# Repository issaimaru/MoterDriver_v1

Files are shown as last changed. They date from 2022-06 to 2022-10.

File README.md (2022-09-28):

# DriveUnit Bseries
**[自作電源基板](https://github.com/Issaimaru/PowerSupply_v1)に刺して使う80A級モータードライバ**<br>
**[DUB with 遠野](https://github.com/Issaimaru/DUB_with_Tono)を使って遠野に刺すこともできます**<br>
**動作電圧 8[V]~30[V]**<br>
**PWM周波数 ~250kHz**<br>
**duty比 100%対応**<br>
**電圧監視機能搭載**<br>
**LAP/SM方式での駆動が可能**<br>
**制作期間:2022/01/18頃～**<br>
**名前:DriveUnit Bseries**<br>

## バージョンに対応するドキュメント
- ver1.0-->[README_v1.md](https://github.com/Issaimaru/MoterDriver_v1/blob/master/README_v1.md)
- ver2.0-->[README_v2.md](https://github.com/Issaimaru/MoterDriver_v1/blob/master/README_v2.md)

## 前モータードライバ(野獣)との違い
野獣がノートパソコンで，DUBがゲーミングパソコンと例えるとわかりやすいと思います．(やや過言かもしれないです...)<br>
野獣ができることは基本的にDUBでもできますし，野獣でできないような機能もDUBにはありますが，値段とサイズ的にはDUBが劣ります．<br>
- **PWM比1.0での動作が可能**<br>
このモータードライバで使用しているA3921というゲートドライバは，ハイサイドにチャージポンプを内蔵しています．そのため，PWM比が1.0の近くであっても正常に動作することができます．<br>

- **動作周波数帯域が増えた**<br>
    > 100Hz以上10000Hz未満なら一応動く。一番特性がいいのは2kHz。<br>
 
  富山本郷メカテック部wikiの野獣の説明にはこのように書いてありますが，20kHzまでは人間の可聴域なので20kHz以下でモータを駆動させると大きな音がモータから発せられてしまいます．      <br>DriveUnit Bseries(以下，DUBといいます．)は ~~**計算上では**100kHzでも動作します．これは実験で確かめます．~~　<br>
  実験したところ，mbedではPWM周波数に比例してPWM分解能が小さくなるため，20kHzを超えると明らかにモーターの動作が不安定になります．
  <br>STM32CubeIDEからHALドライバーを使用し，タイマーの設定を変更することでこの問題を解消することができますが([ここ](https://qiita.com/ShunHattori/items/68f099f1d77702d2535d)を参照)，普通はオンラインコンパイラから制御しますよね...(実際にHALドライバーを使用してやってみましたが色々めんどくさいです)<br>
  上記の問題から，HALドライバーを使用せずにこのモータードライバを使用する場合は10kHz~20kHzで使用することを推奨します．(可聴域内ですが，音は聞こえないです．)<br>
  また，HALドライバーを使用する場合は250kHz以下の周波数で使用するようにしてください．
  
- **LAP/SM方式の切り替えが可能**<br>
このモータードライバで使用しているA3921というゲートドライバの配線をうまくしてやると，PWM方式(LAP/SM)をスイッチ一つで切り替えることが実現できます．SM方式はPWM比がそのまま回転数と比例し，効率がよく，低周波でも線形性が比較的保たれるのに対して，LAP方式は正転と逆転の比率を調整してモータの回転方向と回転速度を変化させる方式であり，Duty比50%でモーターが停止するという違いがあります．

- **定格電圧が大きくなった**<br>
モータードライバでは逆起電力が生じるため加える電圧の2倍程度のマージンを取る必要がある(と他高専のOBの方からアドバイスを頂きました．)<br>そのため， $V_{DS}$ が30 $V$ のFETを使用し，コンデンサやゲートドライバの耐圧も30 $V$ 以上になるように選定しました．<br>また，パスコンには(これも他高専のOBの方のアドバイスで)高分子コンデンサを使用しました．<br>そのため，野獣よりも逆起電力に強くなりましたが，6セルのリポバッテリー等を使って急減速をすると逆起電力で普通に30 $V$ を超えます(上の「特性」を参照)．そのため，6セルのリポバッテリー等を使用する場合は電源ラインをオシロスコープで確認して，逆起電力で30 $V$ を超えないか確認することを推奨します．

- **ボタンでモータを制御できるようになった**<br>
MD10Cのように，ボタンでモータの正転，逆転を制御できるようにしました．

- **定格電流が大きくなった**<br>
DUBでは(これも実験で確かめますが)最大で連続80 $A$ の電流を流すことができます．しかし，ハピロボ以降のロボコンは30 $A$ 以下という電流制限があるため，電源基板側にリセッタブルヒューズがついています．そのためあまり意味はありません．<br>

- **電圧監視機能が付いた**<br>
これもA3921の機能ですが，ハイサイドのFETの $V_{DS}$ 間の電圧を監視することによって万が一短絡した場合でもすぐに動作を止めてくれるほか，オーバーヒートしてるような状態なども検知してFFXのLEDを光らせることで警告してくれます．<br>
A3921のデータシートから取ってきたものですが，各FFピンの出力に対する説明は以下の表の通りとなっています．<br>


- **逆接しにくくなった**<br>
エッジコネクタは物理的に逆接が不可能な状態になっていませんが，野獣は勿論のことこのモータードライバも逆接すると燃えます．<br>
そのため，このモータードライバと電源基板では三角の印をつけることで接続する向きが把握しやすいようにしました．<br>

## はんだ付けの仕方
長くなるのでたたみます．
<details><summary>はんだ付けの仕方</summary>
まず初めに，このモータードライバのはんだ付けはとてもめんどくさいです．<br>
なぜなら，はんだごてではんだ付けするにはあまりにも小さすぎる部品を使っているため，リフローをする必要があるからです(恐らく部内でリフローする基板はこれが初めて)．<br>
といっても，部内にはリフローオーブンなんてないので....<br>

ホットプレートリフロー<br>
ホットプレートを使用したホットプレートリフローではんだ付けしています．<br>
ていっても，基板は両面ありますが片面をホットプレートリフローしてもう片面も同じようにやろうとすると，はんだ付け済みの面が先に温まってしまうので両面をこの方法ですることはできません．そこでもう片面は.......<br>

61UcROmBZZL _SL1500_
ヒートガンを使用したヒートガンリフローではんだ付けしています．<br>
そのため，~~本当にめんどくさい~~ですが一気にはんだ付けできるため手はんだとどっちがめんどくさいかと聞かれるとどっちもどっちかなと思います．<br>
とりあえず，はんだづけの仕方を書いておかないと正直量産は自分以外に難しくなってしまうのでここに書いておきます．<br>

まず，ホットプレートリフローをする面は裏面(下の画像で示している面)です．<br>
<br>

理由は，この基板ではんだ付けが一番難しい部品がこの面のICで，こっちの面をヒートガンでリフローするとリフローの風ではんだが飛んで隣同士がくっついてしまう可能性があるからです．<br>
ホットプレートリフローについては[ここ](https://qiita.com/azusa9/items/a2fc4f26799de5588c58)を見ればやり方は完全理解することができると思いますが，一応自分流のやり方を書いておきます．<br>

1. いらない基板を3つ用意してDUBを囲うように配置する．
    <br>
    画像のように，DUBより大きめの基板をDUBの周りに配置します．<br>

1. テープ(できれば養生)で固定する．
    <br>
    こんな感じでDUBが動かないように固定してください．あとから剥がすので養生の方がいいです．自分は家に養生テープがなかったのでセロハンテープでやってます．

1. ステンシル(メタルマスク)をパッドに合わせて上だけテープで固定する
    <br>
    ステンシルの穴がパッドにしっかりと合うようにして，上だけをテープで固定します．<br>
    上だけを固定する理由は後で説明します．

1. クリーム半田をいらないカード等で伸ばしながら塗る<br>
    
    417DpgW1wLL _AC_<br>
    部室に画像のようなクリームはんだがあると思います．(なければ買ってください．自分は[ここ](https://www.amazon.co.jp/gp/product/B09QCQ12RV/ref=ppx_yo_dt_b_asin_title_o00_s00?ie=UTF8&psc=1)で買いました．)<br>
    これをまずはステンシルに落として，いらないカードなどで伸ばして基板のパッド全てに塗られるようにしてください．<br>
    自分は部室にこれを忘れてきたので塗りませんが，こんな感じです([超簡単、ホットプレートでリフロー（はんだ付け）！](https://qiita.com/azusa9/items/a2fc4f26799de5588c58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)より引用)．<br>

    超簡単、ホットプレートでリフロー（はんだ付け）！より引用<br>

1. ステンシルの上に貼ったテープを支点にステンシルを持ち上げ，部品を乗せる．<br>
    ステンシルの固定の際に上だけをテープで固定した理由はこれを支点にステンシルを持ち上げるからです．<br>
    塗ったクリームはんだを壊さないようにゆっくりと持ち上げたら，いよいよ部品をピンセットで載せていきます．<br>
    ここで注意点をまとめておきます．<br>
    
    - 部品を乗せる際，きっちり押さえつける必要はない．
    - リフローの際に自然にパターンの位置に部品が動くため，多少部品がずれていても修正しない．
    - 特にIC部ははんだが隣同士でくっつくが，修正せずにICを載せる．
    
    以上の注意点を頭に入れながら，部品を載せていきます．<br>
    ちなみに載せるのは表面実装部品のみで，スルーホール部品はまだはんだ付けしません．<br>
    いちいち回路図を参照しながら部品を載せるのはめんどくさいと思うのでここに載せる部品をまとめておきます．(これはver1.0の部品配置です．ver1.0以降のバージョンの部品配置は各ドキュメントに示しておきます．)<br>
    部品配置図(裏面)<br>
    この画像の通りに部品を配置したら，いよいよホットプレートリフローに入ります．<br>

1. ホットプレートリフロー!<br>
    ホットプレートの中心に部品を載せた基板を置き，ホットプレートを加熱していきましょう．部室にあるホットプレートなら中~強の間に合わせればいいと思います．<br>
    そのまま待っていると，煙がでてきてクリームはんだが溶け，金属光沢が現れると思います．全体的にクリームはんだがこの状態になったらホットプレートの加熱をやめ，動かさずに冷えるまで待ってください．<br>
    冷えてはんだが固まったら裏面については終わりです．お疲れ様でした．最後に導通試験をしてください(特にIC)．<br>
    <br>
    **ICの隣同士がくっついていた場合**<br>
    これはよくあります．こうなった場合は，ハンダ吸い取り線で吸い取ってやるとうまく離れると思います．試してみてください．

1. 表面もはんだペーストを塗って部品を配置する<br>
    手順1~5と同様にして表面についてもはんだペーストを塗って，部品を載せます．<br>
    載せる部品をここにまとめておきます．<br>
    ここで，タクトスイッチの裏に丸い突起があるためそのまま置くとパッド面と密着しないと思います．<br>
    そのため突起をニッパー等で取ってから置くようにしてください．<br>

    モータードライバ部品裏面

1. ヒートガンリフロー!<br>
    ヒートガンの風を直にあてて基板を加熱していきます．<br>
    設定は弱風にして，チップLEDの真上にヒートガンがあるようにしてください(チップLEDがヒートガンの風で吹き飛ばされる可能性があるため)．<br>
    このとき，机がヒートガンの熱で壊れる可能性があるので，可能であれば作業マットの上に基板をおいて作業をしましょう．<br>
    この状態でしばらくすると，チップLEDの周りの部品だけはんだが溶けてくると思います．<br>
    はんだが完全に溶けたら，ヒートガンを下にもっていって，タクトスイッチ等についても同様にリフローを行ってください．<br>
    全てのはんだペーストが溶けたら加熱をやめ，動かさずに冷えるまで待ってください．<br>
    冷えてはんだが固まったら表面実装部品のはんだ付けは終わりです．お疲れ様でした．<br>
    <br>
    **タクトスイッチがパッド面と密着せず，リフローに失敗した場合**<br>
    この場合は手はんだではんだ付けしてください．<br>

1. スルーホール部品を手はんだではんだ付けする<br>
    ここまで来たら楽です．あとはいつも通りスルーホール部品をはんだ付けしてください．<br>
    注意点をまとめておきます．<br>
    
    - FETのドレインのピン(3ピンあるうちの真ん中のピン)はニッパーで切る
    - 電解コンデンサは，基板が白で塗りつぶされている方がマイナス(紫色の印がある方)になるように付ける

1. 完成!<br>
    お疲れ様でした．最後に動作試験をしてみてちゃんと動いたらはんだ付けが正しくできています．    

</details>

## 回路図のダウンロード(クローン)方法
1. Gitをインストールします．<br>Gitのインストール方法は[ここ](https://www.sejuku.net/blog/73444)を参照してください．
1. コマンドプロンプトを立ち上げます．
1. `cd ”ダウンロード先フォルダの絶対パス” `<br>
1. `git clone https://github.com/Issaimaru/MoterDriver_v1.git`<br>

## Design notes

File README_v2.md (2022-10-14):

# DriveUnit Bseries(ver 2.0)のドキュメント<br>
ver2.0の使い方，特性などについて解説していきます．<br>
**DIRの入力が反転されているので，ver1.0とは正転，逆転の入力が反対になっています．**<br>
不具合が見つかったら僕に連絡するかIssuesを投げていただけると助かります．

## 基板外形図<br>
**表**<br>
<br>
<br>
**裏**<br>
<br>

基板サイズ:*65.68[mm]×51[mm]*

## ver1.0からの主な修正点
大きな変更から順に書いていきます．<br>
とても細かい変更も一応書いておきます．<br>
1. 入力が浮いても暴走しなくなった<br>
これが一番大きな改善点です．<br>
ロボコンにおいて恐らくロボットの暴走が一番避けたいことだと思うので...(ver1.0を使用していたときは別に暴走対策用の回路を作っていました)<br>

1. DIRの入力をゲートドライバICに合わせた<br>
ver1.0と同じ入力になるように組むよりも，PWMと同様にDIRの入力も反転したほうが部品点数が少なく済むなどのメリットがあったため，DIRも入力を反転しました．<br>
(絶縁用のフォトカプラで更に入力が反転されるので)結果的に，ゲートドライバICに入力されている信号はこのモータードライバに入力している信号と一致します．<br>
そのため，前モータードライバと異なりDIRが1で正回転，0で負回転です．<br>

1. ボタン入力が優先になった<br>
ver1.0はボタン入力とマイコン入力の優先順位が同じだったため，マイコン入力が特定の状態でないとボタンが正常に動かない~~クソ仕様~~でした．<br>
そのため今回の回路ではマイコン入力が任意の状態でもボタンが正常に動くように回路を組み直しました．<br>

1. ボタンとスライドスイッチの位置を逆にした<br>
ボタンを上から押しやすくするため，スライドスイッチよりも上にボタンを配置しました．

1. SAとSB，FF1とFF2の位置を逆にした<br>
ver1.0はFF1とFF2の位置がデータシートのFault Definitionsに載っている順と逆に書いてしまったため，エラーを吐いた時に間違えやすく，さらにシルクが小さすぎてどのLEDがFF1か分からなくなっていたため~~本当にゴミ~~でした．<br>
SAとSBについても，ボタンの配置と逆にしていたので左のボタンを押すと右のLEDが光るという仕様になっていました．<br>
そのため，これらのLEDの位置を逆にしました．

1. シルクとQRコードを大きくして読みやすくした<br>
シルクが小さすぎてはんだ付けの際やLEDを見る際などに非常に不便だったのでシルクを全体的に大きくしました．<br>
また，基板裏面のQRコードはアプリを使用すると(恐らくQRコードの補完機能で)読み取れるのですが，IPhoneのカメラアプリなどを使用して読み取ろうとする人が読み取れないと言っていたのでQRコードも大きくしました．<br>

1. ICの背面パッドをGNDに接続するようにした<br>
ICの背面パッドは放熱を良くするため，GNDのインピーダンスを低くするために設けられているのですが，ver1.0ではそれ用のパッドをつけ忘れてしまいICの背面パッドを基板に接続することができませんでした．<br>
今回は背面パッド用のGNDパッドを基板に設けてあるので基板に接続することができます．<br>

## 使い方
ver1.0の共通点が多々あるので所々コピペしますが一応ver1.0のドキュメントを参照しなくてもわかるようにします．<br>
また，ver1.0と違うところはわかりやすいように💫で示します(~~きれい~~)．<br>
前モータードライバ(野獣)にはない機能があるので使用者は必ず確認してください．<br>
長くなるため折りたたみます．
<details><summary>使い方</summary>
  
  まずはLAP/SM切り替えスイッチについて説明していきます．
  - LAP/SM切り替えスイッチ
  <br>
  このスイッチは名前の通り，LAP方式とSM方式を切り替えることできるスイッチです．<br>
基板にあるシルクの通り，スライドスイッチを"SM"の文字の方にスライドするとSM方式，"LAP"の文字の方にスライドするとLAP方式となります．<br>
SM方式を採用する場合にはPWMピンにはPWM信号を流し，DIRピンには回転方向の信号を流してください(下の表参照)<br>
LAP方式を採用する場合はPWMピンには何も繋げずに**DIRピンに**PWM信号を流してください．<br>
LAP/SM方式の場合の各ピンの真理値表は以下のようになっています．<br>

    |PWM|DIR|出力(SM)|
    |:---:|:---:|:---:|
    |1~100%|0|負回転💫|
    |1~100%|1|正回転💫|
    |0%|$\phi$|ブレーキ|

    |DIR|出力(LAP)|
    |:---:|:---:|
    |0~49%|負回転💫|
    |50%|無回転|
    |51~100%|正回転💫|

    LAP方式とSM方式の違いは[このページ](https://note.suzakugiken.jp/motordriver-sm-and-lap-tutorial-a/)を参照してください．<br> 
    安全性や効率の観点から基本的にはSM方式を採用してください．

- 手動・テストボタン
    <br>
  
    このボタンを押すことで手動でモーターを動かすことができます．<br>
    モータが駆動しないとき，このモータードライバの問題かその他の問題かを判別したり，機構がちゃんと動くかのテスト等に活用してください．<br>
    SAボタンを押すと正回転，SBボタンを押すと負回転になります．<br>
    💫PWM信号による入力よりもボタン入力が優先になっています．<br>
    💫LAP方式でもこのボタンを使用することができます．

- ファルトフラグ，RESETボタン
    <br>

    このLEDが光っているということはなにかこのモータードライバに不具合があるということです．<br>
    なんの不具合があるかは下の表を参考にしてください．<br>

    <br>

    ちなみに，この表のFault LatchedにYesがついているエラーは，もしエラーの状態が治ったとしてもリセットボタンを押さないとエラーが出力されたまま動作しなくなるので，リセットボタンを押してください．<br>
    
    また，この表だけじゃ情報不足でわからないと思います．<br>全部英語ですがA3921のデータシートのp12~p13に乗っています．A3921のデータシートは[公式サイト](https://www.allegromicro.com/ja-jp/products/motor-drivers/brush-dc-motor-drivers/a3921/)からダウンロードしてください．<br>
    ちなみに，このモータードライバを設計するときにA3921のデータシートを読むモチベのためにQiitaで記事を書いたので，A3921を使いたい!みたいなことがあれば[ここ](https://qiita.com/issaimaru/items/3c1aff6e6718ecfb7793)から飛んでください．<br>

    <br>

    リセットボタンを押すとA3921がスリープモードに入り，動作しなくなります．(離すと再び動作します．)<br>
    スリープモードに入ることで，A3921が検知していた異常が全てリセットされます．<br>

- 回転方向表示LED
    <br>

    このLEDの表示を見ることで，モータがどちらの方向に回転しているかを知ることができます．<br>
    PowerUnit BseriesのOUT+の電位がOUT-よりも高くなっているときのモータの回転方向を正とすると，SAが光っているときは正回転を，SBが光っているときは負回転をしています．<br>
    ちなみに，SM方式の場合は片方のみLEDが光りますが，LAP方式の場合は両方のLEDが光るはずです．<br>
    LAP方式の場合はLEDの光の強さで回転方向を読み取ってください．(SAの光の方が強ければ正回転，SBの光の方が強ければ負回転です．)<br>

- 電源表示LED

    <br>
    DUBがちゃんと電源に接続されているなら，このLEDが光っているはずです．<br>
    PowerUnit Bseriesか遠野に挿している場合で，電源に接続しているのにこのLEDが光らない場合は非常停止スイッチが接続されていない可能性があります．<br>
    PowerUnit Bseriesか遠野の「SWITCH」に非常停止スイッチがしっかりと接続されているかを確認してください．<br>

 - GitHub QRコード

    <br>

    ~~このページにアクセスしているということはこのQRコードから飛んできたということは置いといて~~一応説明しておきます．<br>
     このQRコードを読み込むことでこのページに飛ぶことができます．<br>
    使用前には極力このページに飛んで仕様を再確認しておくと良いでしょう．<br>
    ちなみに，レポジトリ名が「DriveUnit Bseries」ではなく「MoterDriver_v1」なのはリポジトリ名を変更するとURLが変更されるためこのQRコードからこのページに飛ぶことができなくなるからです......(ver2.0なのにMoterDriver_v1???)

    基本的には以上がver2.0のDUBの機能です．<br>
    機能など，このモータドライバについて質問があれば何らかの手段で僕に連絡していただければ答えます．<br>

</details>

## 使い方(応用編)
ここからは抵抗値をいじって変えるような設定の変更方法等を書いていきます．<br>
なので回路班の方が見ることを想定しています．<br>
長くなるので折りたたみます．
<details><summary>使い方(応用編)</summary>

  - デッドタイムの調整<br>
    このモータードライバはデッドタイムを変更することができます．<br>
    どこで変えることができるかというと，R13の抵抗値を変えることで変更することができます．<br>
    R13には3kΩから240kΩまでの2012サイズのチップ抵抗を接続してください．<br>
    デッドタイムとR13の抵抗値の関係は次の近似式で計算することができます．<br>
  
    $$
    t_{DEAD}(nom)=50+\frac{7200}{1.2+\frac{200}{R_{DEAD}}}
    $$
  
    ここで， $R_{DEAD}$ の単位は[kΩ]， $t_{DEAD}$ の単位は[ns]です．<br>

  - 短絡検出の基準電圧の調整<br>
    このモータードライバはハイサイドのFETがオンになっているときの電圧を監視してその値がゲートドライバICのVDSTHピンに入力されている電圧よりも高ければ短絡していると判断しエラーを出力しています．<br>
    まず，正常の場合は下記の画像のように電圧降下が殆どモータで起きるのでハイサイドのFETでの電圧降下は非常に小さいです．<br>
    MD説明_正常ver<br>
    次に，短絡している場合は下記の画像のようにモータを介さずに電流が流れるためFETでの電圧降下が非常に大きくなります．<br>
    MD説明_短絡ver<br>
    この仕組みを利用して短絡検出を行っていますが，VDSTHピンに入力される電圧が大きすぎても短絡が検出されにくくなり，逆に小さすぎても短絡してないときにエラーが発生する可能性が出てきてしまうため，VDSTHに入力する電圧の検討は重要です．<br>
    VDSTHに入力する値はR2，R14の抵抗値を調整することで変更することが可能であり，内部で以下のような回路になっています．<br>
    <br>
    ここで，2.2kΩの方がR14，3.3kΩの方がR2です．<br>
    式で書いたほうがわかりやすいと思うので...<br>
  
    $$
    V_{DSTH}=5\times\frac{R2}{R2+R14}
    $$
  
    で求められます．<br>
    ここで，V5ピンから出力される電流を小さくするためR2とR14には大きな値の抵抗を使用することを推奨します．<br>
    > **Note** <br>
    > 出力の大きいモータのduty比を0%から100%に急にすると大電流が流れるためこの短絡検出機能が作動してしまうことがあります．<br>
    > その場合はR14の抵抗を0[Ω]抵抗に変えることでこの短絡検出機能を無効にすることができます．
    
</details>

## 使用電子部品，値段
  部品の値段は頻繁に変動するため示さないことにしましたが，ver1.0と同じ部品をほぼ同じ量使用しているため値段はver1.0より少し高いくらいだと思います．<br>
  チップ抵抗は特性等あまり重要でないので2012サイズの同じ値の抵抗なら何でも大丈夫ですが，コンデンサはDCバイアス等を考慮しているためここに示されているものと同じものを使用することを強く推奨します．<br>

  |部品番号|部品名称|リンク|個数|
  |:---------:|:---:|:---:|:---:|
  |IC1|A3921KLPTR-T|https://www.digikey.jp/en/products/detail/A3921KLPTR-T/620-1523-6-ND/4318336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|1個|
  |3813-XX|IRLB3813PBF|https://akizukidenshi.com/catalog/g/gI-06270/|4個|
  |SW1，SW2|TVAF06-A020B-R|https://akizukidenshi.com/catalog/g/gP-14888/|2個|
  |SW3|THAF01-NC-R|https://akizukidenshi.com/catalog/g/gP-14887/|1個|
  |SW4|SS-12D00G3|https://akizukidenshi.com/catalog/g/gP-15707/|1個|
  |TRX|2SC3325|https://akizukidenshi.com/catalog/g/gI-00628/|4個|
  |TLPX|TLP2366|https://akizukidenshi.com/catalog/g/gI-11342/|2個|
  |LED1，LED2|SML-E12P8WT86(緑)|https://akizukidenshi.com/catalog/g/gI-11878|2個|
  |LED3|SML-E12Y8WT86|https://akizukidenshi.com/catalog/g/gI-11880|1個|
  |LED4，LED5|SML-E12V8WT86|https://akizukidenshi.com/catalog/g/gI-11879|2個|
  |DX|GS1010FL|https://akizukidenshi.com/catalog/g/gI-06014/|5個|
  |C1，C2，C3，C4，C5，C7，C8|GCM188L81H104KA57D|https://www.digikey.jp/en/products/detail/murata-electronics/GCM188L81H104KA57D/2591908|7個|
  |C6|GCM21BR71H474KA55L|https://www.digikey.jp/ja/products/detail/murata-electronics-north-america/GCM21BR71H474KA55L/1641707|1個|
  |C9|GRT31CC81H225KE01L|https://www.digikey.jp/ja/products/detail/murata-electronics/GRT31CC81H225KE01L/5416844|1個|
  |C10，C11|35PZJ330M10X9|https://akizukidenshi.com/catalog/g/gP-16867/|2個|
  |C12|GRM32ER71H106KA12|https://akizukidenshi.com/catalog/g/gP-16113/|1個|
  |C13|GRM21BC72A105KE01|https://akizukidenshi.com/catalog/g/gP-13699/|1個|
  |R1，R4，R5，R6，R9，R11，R15，R16，R17，R18，R19，R24，R25|RG2012-N-103-B-T5|https://akizukidenshi.com/catalog/g/gR-11797/|13個|
  |R2|RG2012N-332-W-T1|https://www.digikey.jp/ja/products/detail/susumu/RG2012N-332-W-T1/600888|1個|
  |R3，R22|RG2012P-681-B-T5|https://www.digikey.jp/ja/products/detail/susumu/RG2012P-681-B-T5/1266877|2個|
  |R7，R8，R26，R27|RG2012N-201-W-T1|https://www.digikey.jp/ja/products/detail/susumu/RG2012N-201-W-T1/600671|4個|
  |R10，R12，R20，R21|RG2012Q-100-D-T5|https://jp.rs-online.com/web/p/surface-mount-resistors/6379813|4個|
  |R13|RG2012P-302-B-T5|https://www.digikey.jp/ja/products/detail/susumu/RG2012P-302-B-T5/1240739|1個|
  |R14|RG2012N-222-W-T1|https://www.digikey.jp/en/products/detail/susumu/RG2012N-222-W-T1/600696|1個|

<details><summary>回路図(Eagle)</summary>

  DriveUnit_ver2 0

</details>

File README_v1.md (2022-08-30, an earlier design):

# DriveUnit Bseries(ver 1.0)のドキュメント<br>
ver1.0の使い方，特性などについて解説していきます．<br>
最初のバージョンなのでガバが多少見つかりました．<br>
このドキュメントに書いてあること以外でこのバージョンにおけるガバが見つかれば僕に連絡するかIssuesを投げていただけると助かります．

## 基板外形図<br>
**表**<br>
DriveUnit_B-series(ver1 0)<br>
<br>
**裏**<br>
DriveUnit_B-series(ver1 0)<br>

基板サイズ:*65.68[mm]×51[mm]*

## 使い方
野獣にはない機能があるので使用者は必ず確認してください．
長くなるため折りたたみます．
<details><summary>使い方</summary>

まずはLAP/SM切り替えスイッチについて説明していきます．
- LAP/SM切り替えスイッチ

このスイッチは名前の通り，LAP方式とSM方式を切り替えることできるスイッチです．<br>
基板にあるシルクの通り，スライドスイッチを"SM"の文字の方にスライドするとSM方式，"LAP"の文字の方にスライドするとLAP方式となります．<br>
SM方式を採用する場合にはPWMピンにはPWM信号を流し，DIRピンには回転方向の信号を流してください(下の表参照)<br>
LAP方式を採用する場合はPWMピンには何も繋げずに**DIRピンに**PWM信号を流してください．<br>
LAP/SM方式の場合の各ピンの真理値表は以下のようになっています．<br>
    
    |PWM|DIR|出力(SM)|
    |:---:|:---:|:---:|
    |1~100%|0|正回転|
    |1~100%|1|負回転|
    |0%|$\phi$|ブレーキ|

    |DIR|出力(LAP)|
    |:---:|:---:|
    |0~49%|正回転|
    |50%|無回転|
    |51~100%|負回転|
    
    ※LAP方式についてはMD10C等一般的なモータードライバと正転・逆転が逆だと思うので注意してください．<br><br>
    LAP方式とSM方式の違いは[このページ](https://note.suzakugiken.jp/motordriver-sm-and-lap-tutorial-a/)を参照してください．<br> 
    安全性や効率の観点から基本的にはSM方式を採用してください．
    
- 手動・テストボタン
    
    
    このボタンを押すことで手動でモーターを動かすことができます．<br>
    モータが駆動しないとき，このモータードライバの問題かその他の問題かを判別したり，機構がちゃんと動くかのテスト等に活用してください．<br>
    SAボタンを押すと正回転，SBボタンを押すと負回転になります．<br>
     **このボタンを使用する際にはPWMピンをLOW，DIRピンをHIGHにして使ってください．それ以外の場合は正常に動作しません．**

    > **Warning** <br>
    >LAP方式の場合はSAボタンで正回転，負回転を一応切り替えられますが，モーター及びDUBに極めて大きい負荷がかかるため非推奨
    
- ファルトフラグ，RESETボタン
    
    <br>
    

    このLEDが光っているということはなにかこのモータードライバに不具合があるということです．<br>
    なんの不具合があるかは下の表を参考にしてください．<br>
    <br>
    
    ちなみに，この表のFault LatchedにYesがついているエラーは，もしエラーの状態が治ったとしてもリセットボタンを押さないとエラーが出力されたまま動作しなくなるので，リセットボタンを押してください．<br>
    
    また，この表だけじゃ情報不足でわからないと思います．<br>全部英語ですがA3921のデータシートのp12~p13に乗っています．A3921のデータシートは[公式サイト](https://www.allegromicro.com/ja-jp/products/motor-drivers/brush-dc-motor-drivers/a3921/)からダウンロードしてください．<br>
    ちなみに，このモータードライバを設計するときにA3921のデータシートを読むモチベのためにQiitaで記事を書いたので，A3921を使いたい!みたいなことがあれば[ここ](https://qiita.com/issaimaru/items/3c1aff6e6718ecfb7793)から飛んでください．<br>
    リセットボタンを押すとA3921がスリープモードに入り，動作しなくなります．(離すと再び動作します．)<br>
    スリープモードに入ることで，A3921が検知していた異常が全てリセットされます．<br>
    
- 回転方向表示LED
    <br>
    このLEDの表示を見ることで，モーターがどちらの方向に回転しているかを知ることができます．<br>
    PowerUnit BseriesのOUT+の電位がOUT-よりも高くなっているときの回転方向を正とすると，SAが光っているときは正回転を，SBが光っているときは負回転をしています．<br>
    ちなみに，SM方式の場合は片方のみLEDが光りますが，LAP方式の場合は両方のLEDが光るはずです．<br>
    LAP方式の場合はLEDの光の強さで回転方向を読み取ってください．(SAの光の方が強ければ正回転，SBの光の方が強ければ負回転です．)<br>
    
- 電源表示LED

    <br>
    DUBがちゃんと電源に接続されているなら，このLEDが光っているはずです．<br>
    PowerUnit Bseriesか遠野に挿している場合で，電源に接続しているのにこのLEDが光らない場合は非常停止スイッチが接続されていない可能性があります．<br>
    PowerUnit Bseriesか遠野の「SWITCH」に非常停止スイッチがしっかりと接続されているかを確認してください．<br>
    
 - GitHub QRコード
    <br>
    ~~このページにアクセスしているということはこのQRコードから飛んできたということは置いといて~~一応説明しておきます．<br>
    このQRコードを読み込むことでこのページに飛ぶことができます．<br>
    使用前には極力このページに飛んで仕様を再確認しておくと良いでしょう．<br>
    ちなみに，レポジトリ名が「DriveUnit Bseries」ではなく「MoterDriver_v1」なのはリポジトリ名を変更するとURLが変更されるためこのQRコードからこのページに飛ぶことができなくなるからです......(ver1.0以降どうするんだこれ...)
    
    基本的には以上がver1.0のDUBの機能です．<br>
    機能など，このモータドライバについて質問があれば何らかの手段で僕に連絡していただければ答えます．<br>
    
</details>

## 特性
このモータードライバの特性についてはここに示します．<br>
~~どちらかというとモーターの特性になってるかもしれないです．~~<br>
これも長くなるため折りたたみます．  
<details><summary>ver1.0の特性</summary>

- 逆起電力の特性<br>
    >使用モータ:RS-555VC-5524<br>
    >使用マイコン:NUCLEO-F401RE<br>
    >印加電圧:12V<br>
    >PWM方式:Sign Magnitude(SM)<br>
    >PWM周波数:10kHz

    上記のものを使用してこの特性の調査を行いました．<br>
    また，調査の流れとしてはマイコンとこのモータードライバを使って一定のペース(これをx[ $ms$ ]とします)で加速→定格(12V)で運転→急減速の流れでモータを運転し，急減速の際の電源ラインの波形を読み取る，といった感じです．<br>

    - x=100の時の波形<br>
        x=100<br>
        画像の通り，リップルは発生してないです．

    - x=50の時の波形<br>
        x=50<br>
        最大で電源ラインが15Vになっています．

    - x=25の時の波形<br>
        x=25<br>
        最大で電源ラインが23V程度になっています．

    - x=13の時の波形<br>
        x=13<br>
        最大で電源ラインが28V程度になっています．

    - x=7の時の波形<br>
        x=7<br>
        x=13の時と同様に最大で電源ラインが28V程度になっています．
    - x=3の時の波形<br>
        x=3<br>
        x=7の時に比べるとかなり発生する逆起電力が小さくなっていることがわかります．
    - x=0の時の波形<br>
        x=0<br>
        逆起電力が見られなくなりました．(多分回生ブレーキに使われるから？)

    ちなみに野獣でも同じ条件でこの実験をすると，最大の電源ラインの電圧はほぼ変わりませんでしたが，野獣は耐圧がこのモータードライバよりも低いため逆起電力で壊れる可能性があります．(実際に実験の最中に壊れました...)<br>
    なので，急停止するような動作が必要な場合には12[ $V$ ]でもこのモータードライバを使用することを推奨します．<br>

- 周波数-回転数特性
    >使用モータ:RS-555VC-5524<br>
    >使用マイコン:NUCLEO-F401RE，NUCLED-F411RE<br>
    >印加電圧:12V<br>
    >PWM方式:Sign Magnitude(SM)<br>

    上記のものを使用してこの特性の調査を行いました．<br>
    また，調査の流れとしては特定のPWM周波数(これをfとします．)で，0[ $V$ ]から10[ $s$ ]で定格(12V)になるようにduty比を一定間隔で増やしているPWM信号をこのモータードライバに送り，エンコーダから算出した回転数をマイコンからPCにprintfで出力しTera Termから値を読み取ってそれを折れ線グラフにします．<br>
    このとき，モータを駆動するマイコンと，エンコーダのパルスを読み取り回転数をprintf出力するマイコンを分けているため，printfの処理時間等は以下のグラフで見られる非線形性の要因とは無関係と言えます．

    - f=500Hz<br>
        500Hz<br>
    
    - f=1kHz
        1kHz

    - f=2kHz
        2kHz

    - f=5kHz
        5kHz

    - f=10kHz
        10kHz

    - f=20kHz(HAL不使用)
        20kHz(HAL不使用)<br>
        グラフを見てわかるように，20kHzになるとギザギザなグラフになっており，線形性が保たれていません．<br>
        これはPWM分解能が落ちている証拠です．なので，これ以降はHALを用いて計測していきます．<br>
        
    - f=20kHz(HAL使用)
        20kHz(HAL使用)
        
    - f=40kHz
        40kHz

    - f=80kHz
        80kHz<br>
        周波数が増えるにつれて，duty比が大きいところの線形性が保たれなくなってきています．
        
    - f=160kHz
        160kHz

    - f=250kHz(最大)
        250kHz
        
        グラフから，明らかに周波数が増えるにつれてduty比が0.9程度のところで回転数が一度落ちています．<br>これの原因は不明ですが，モーターの出力をオシロスコープで確認すると回転数が落ちるところで周波数が3kHz程度まで落ちることから，ブートストラップからチャージポンプに昇圧方式を変える時にコンデンサの容量が異なることでなにか問題が起きていると考えられます．<br>
        また，モータの両端にプロープをつけて波形を見てみたところ，ギブス現象の正弦波4本程度で矩形波を近似したときのような波形が得られ，電流が振動していました．<br>
        とりあえず，10kHzが一番線形性が保たれており，効率もいいので10kHzで使用するのが一番いいということがグラフから読み取れます．(あくまでこれは，RS555の場合です．)<br>
        <追記>RS-775を同じように250kHzで回してもギブス現象のような波形が得られず与えたPWM波形と同じ波形を出力していたことから，これはモータ側の問題であることが分かりました．~~しかし，duty比が0.9程度のところで回転数が落ちるのはこのモータードライバの問題のようです．~~<br>
        <追記>実験をしたところ，モータを接続したときのみ(高周波では)duty比0.9以上で電圧が12Vから10Vに落ち，またRS-775に変えるとこのような現象は起こらなかったことから，これもモータが原因だと思われます．<br>

</details>
          
## 現在分かっている設計のガバ

**使用者は必ずこれを見てください!!**

基板を発注する前にブレッドボードで回路が正しいかを確認するのが普通なのですが，A3921が極めて小さくて手はんだできないのもあり，実はブレッドボードで試作せずに基板を発注しています．<br>
しかも，A3921周りの回路は参考にできる記事や回路が見つからず，殆ど自分で組んでいます．<br>
そのため，実際に動かしてみてわかった設計のガバが少しあったのでそれを書いていきます．<br>
また，このガバは極力バージョンアップで無くしていきます．<br>

- 入力が浮くと全力で正回転する<br>
    マイコン側にノイズがいかないようにするためにフォトカプラで信号の入力線を絶縁しているのですが，フォトカプラはTLP2366(またはTLP2367)を使用していて，このフォトカプラは内部でNOTがかかり，内部のLEDが光っている(信号が入力されている)時にLOW，内部のLEDが光っていない(信号が入力されていない)時にHIGHになります．<br>
    従って，普通に繋ぐとPWM信号がHIGHの時にLOW，PWM信号がLOWの時にHIGHとなってしまい，仮にDuty比を20%にすると80%の出力になるため，制御性が悪くなってしまいます．<br>
    そのために，下の画像のようにマイコンのVCCとPWMピンに繋げることで，フォトカプラのNOTを打ち消すNOTを掛け，PWM信号が0の時に入力が0，PWM信号が1の時に入力が1となるようにしています．(DIRを反転していないのはA3921が「1で正転，0で逆転」になり，これは前モータードライバと逆であるので，前モータードライバと同じ入力で正転となるようにするためです．)

    <br>
    
    ※修正前の回路なのでフォトカプラのLEDに抵抗が付いていませんが，実際には付いています．<br>
    <br>
    ここで，マイコンからの信号線を取り外し，入力が浮いている状態を考えてみましょう．<br>
    入力が浮いているので内部のLEDは当然光りません．<br>
    すると，下の画像のようにPWMへの入力が1になってしまいます．<br>
    すなわち，この状態で電圧をかけるとモータが全力で回転し始めます．

    <br>

    これが，１つ目のガバです．<br>
    ロボットが暴走する原因になるので，以下のことを絶対に守ってください．<br>

    - マイコンをリセットする際は非常停止スイッチを押してからリセットを行う．
    - 入力を浮かせた状態でこのモータードライバを使用しない．
    
    ただ，以下のように回路を組めばこのガバをなくすことができます．<br>
    
    <details><summary>リセット時に暴走するガバを修正する回路</summary>
    
    

    </details>

    ちなみに，このガバは出力がNOTではないフォトカプラを選べばいいのですが，高速なフォトカプラは自分が探した限り全て出力がNOTで，これを低速なものに変えると前モータードライバと同じくらいの周波数までしか対応できなくなることが予想されます．

- ボタンスイッチを使用できる入力の状態が制限されている<br>
    これも上記のガバに関連しているのですが，ボタンスイッチを正常に使用できるのは**入力が浮いていない状態で，PWMピンが0，DIRピンが1である状態です．**<br>
    このときの内部の状態は下の画像のようになっています．<br>
    <br>

    入力が，浮いている状態を含むその他の状態ではPWMやDIRに既に1が入ってしまうので，SW1を押すと正転，SW2を押すと逆転，といった正常な動作をすることができなくなります．<br>
    けど，このスイッチの需要って大体入力が浮いている時，すなわちDIRとPWMが1の時にあると思うので....<br>
    回路の組み方を変えて全力で回転する問題と一緒に治す予定です．

## 使用電子部品，値段
チップ抵抗等大量に使用する部品の場合は1個あたりの値段を算出し，値段の横に個数を括弧で示します．<br>
又，同様の部品がある場合は部品番号をXと表記し，まとめて示します．<br>(例:3813-HA，3813-LAはどちらもIRLB3813PBFを使用しているため部品番号を3813-XXと示します．)<br>
|部品番号|部品名称|リンク|値段(一個)|
|:---:|:---:|:---:|:---:|
|IC1|A3921KLPTR-T|https://www.digikey.jp/en/products/detail/A3921KLPTR-T/620-1523-6-ND/4318336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|¥476.3(10個)|
|3813-XX|IRLB3813PBF|https://akizukidenshi.com/catalog/g/gI-06270/|￥140 × 4|
|SW1，SW2|TVAF06-A020B-R|https://akizukidenshi.com/catalog/g/gP-14888/|￥22 × 2(5個)|
|SW3|THAF01-NC-R|https://akizukidenshi.com/catalog/g/gP-14887/|￥24(5個)|
|SW4|SS-12D00G3|https://akizukidenshi.com/catalog/g/gP-15707/|￥20|
|TRX|2SC3325|https://akizukidenshi.com/catalog/g/gI-00628/|￥5 × 2(20個)|
|TLPX|TLP2366|https://akizukidenshi.com/catalog/g/gI-11342/|￥120 × 2|
|LED1，LED2|SML-E12P8WT86(緑)|https://akizukidenshi.com/catalog/g/gI-11878|￥10 × 2(10個)|
|LED3|SML-E12Y8WT86|https://akizukidenshi.com/catalog/g/gI-11880|￥10(10個)|
|LED4，LED5|SML-E12V8WT86|https://akizukidenshi.com/catalog/g/gI-11879|￥10 × 2(10個)|
|DX|GS1010FL|https://akizukidenshi.com/catalog/g/gI-06014/|￥10 × 3(10個)|
|C1，C2，C3，C4，C5，C7，C8|GCM188L81H104KA57D|https://www.digikey.jp/en/products/detail/murata-electronics/GCM188L81H104KA57D/2591908|￥11.5 × 7(100個)|
|C6|GCM21BR71H474KA55L|https://www.digikey.jp/ja/products/detail/murata-electronics-north-america/GCM21BR71H474KA55L/1641707|￥26.2(10個)|
|C9|GRT31CC81H225KE01L|https://www.digikey.jp/ja/products/detail/murata-electronics/GRT31CC81H225KE01L/5416844|￥39.4(10個)|
|C10，C11|35PZJ330M10X9|https://akizukidenshi.com/catalog/g/gP-16867/|￥90 × 2|
|C12|GRM32ER71H106KA12|https://akizukidenshi.com/catalog/g/gP-16113/|￥40(5個)|
|C13|GRM21BC72A105KE01|https://akizukidenshi.com/catalog/g/gP-13699/|￥15(10個)|
|R1，R9，R11，R15，R16，R18，R19|RG2012-N-103-B-T5|https://akizukidenshi.com/catalog/g/gR-11797/|￥20 × 7(5個)|
|R2|RG2012N-332-W-T1|https://www.digikey.jp/ja/products/detail/susumu/RG2012N-332-W-T1/600888|￥107.9(10個)|
|R3，R22|RG2012P-681-B-T5|https://www.digikey.jp/ja/products/detail/susumu/RG2012P-681-B-T5/1266877|￥36.7 × 2(10個)|
|R5，R6|RG2012-N-102-B-T5|https://akizukidenshi.com/catalog/g/gR-11796/|￥20 × 2(5個)|
|R4，R7，R8，R17|RG2012N-201-W-T1|https://www.digikey.jp/ja/products/detail/susumu/RG2012N-201-W-T1/600671|￥107.9 × 4(10個)|
|R10，R12，R20，R21|RG2012Q-100-D-T5|https://jp.rs-online.com/web/p/surface-mount-resistors/6379813|￥47 × 4(50個)|
|R13|RG2012P-302-B-T5|https://www.digikey.jp/ja/products/detail/susumu/RG2012P-302-B-T5/1240739|￥48.7(10個)|
|R14|RG2012N-222-W-T1|https://www.digikey.jp/en/products/detail/susumu/RG2012N-222-W-T1/600696|￥107.9(10個)|
|総額|||￥2972.9
          
<details><summary>回路図(Eagle)</summary>

  schematic edit 
    
</details>

今見つかっている不具合はこんなところです．<br>
このモータードライバを使用して何か不具合などが出てきたら教えてくださると助かります．

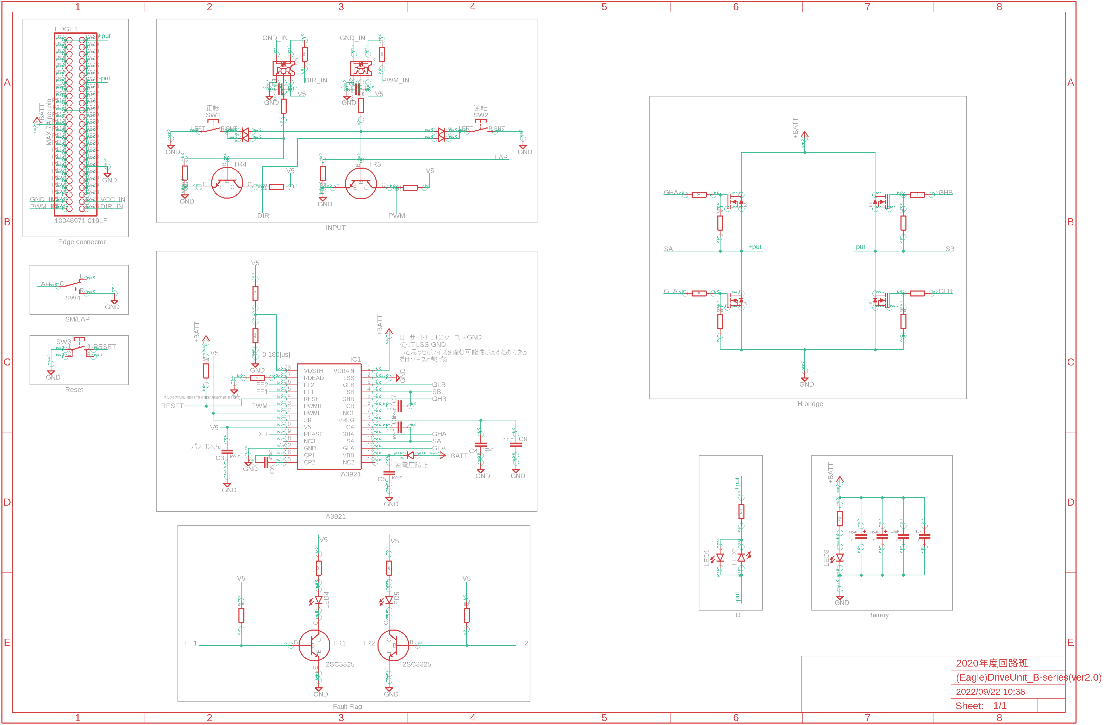
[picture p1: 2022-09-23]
src/Eagle image/DriveUnit_ver2.0.png

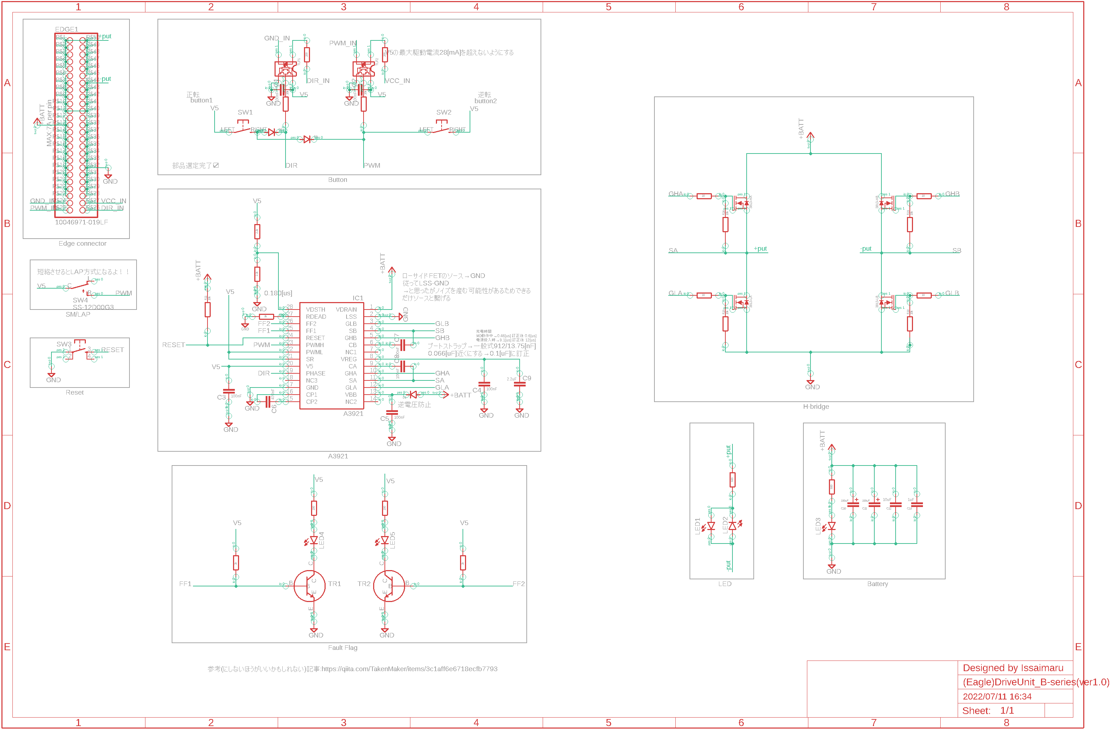
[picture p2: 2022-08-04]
src/Eagle image/DriveUnit_ver1.0.png

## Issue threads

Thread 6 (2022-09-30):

ver2.0における不具合，設計のガバ

Issaimaru, 2022-09-30:
またしてもガバ.....
- トランジスタのベースにスピコンつけなかったことにより，30kHzを超えると並列にスピコンをつけないと遅延が目立つ

Issaimaru, 2022-10-14:
デジタルアイソレータ，使おう!

Issaimaru, 2022-10-14:
https://www.digikey.jp/ja/products/detail/skyworks-solutions-inc/SI8622BB-B-ISR/7201599<br>
これとかどう？

Issaimaru, 2022-11-12:
チップMOSFET使っても直らなかったのでますますデジタルアイソレータ使いましょうね

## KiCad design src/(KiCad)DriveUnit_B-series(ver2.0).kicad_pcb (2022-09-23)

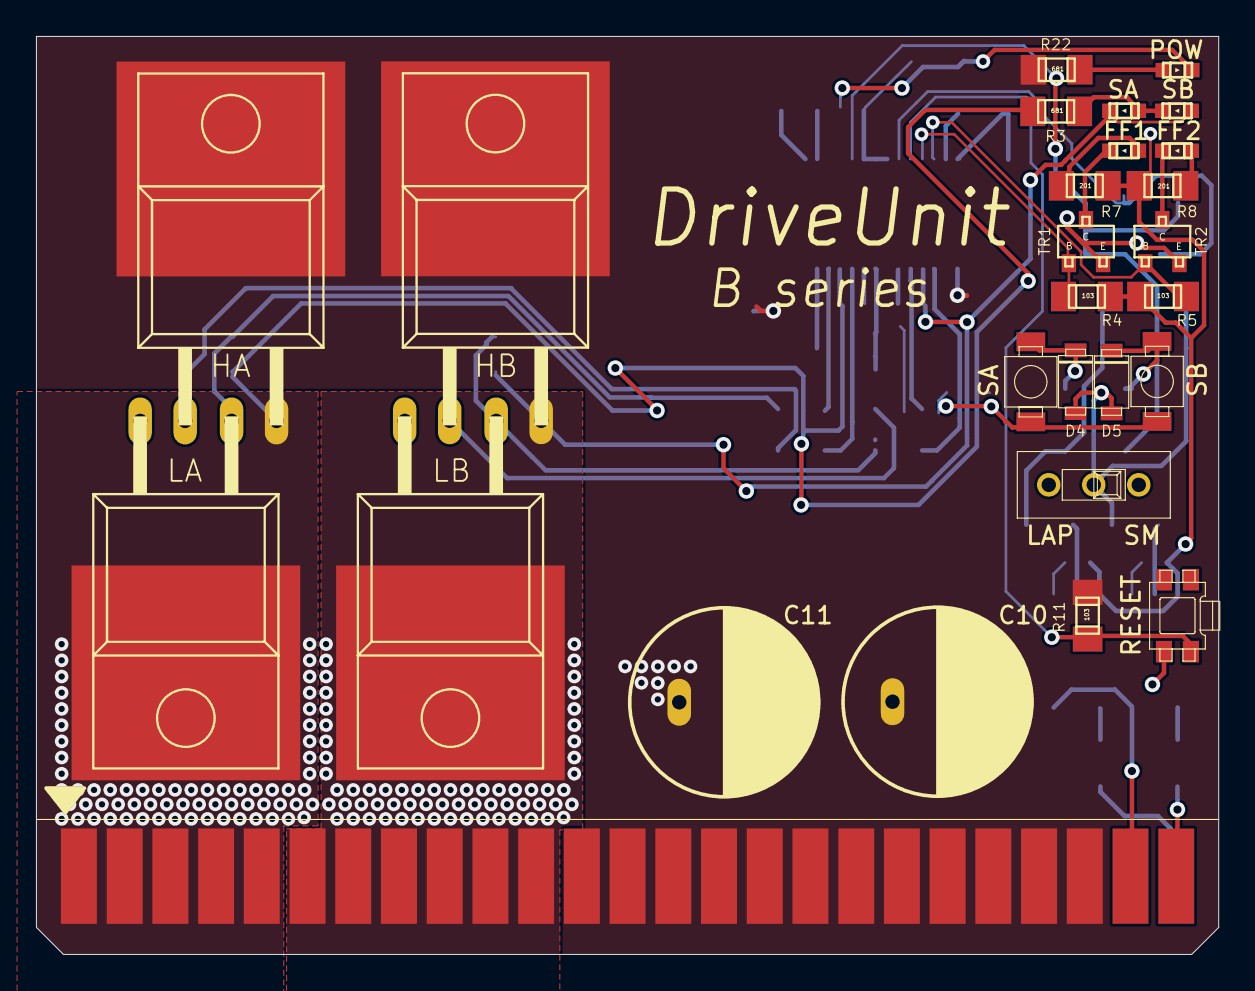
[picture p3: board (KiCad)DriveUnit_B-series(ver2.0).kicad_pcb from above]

Board: 2 copper layers, 65.7 x 51.0 mm, 65 parts (0 on the bottom side), 43 nets.

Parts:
A3921: A3921
C1, C2, C3, C4, C5, C7, C8: GCM188L81H104KA57
C6: GCM21BR71H474KA55
C9: GRT31CC81H225KE01L
C10, C11: 35PZJ330M10X9
C12: GRM32ER7YA106KA12
C13: GRM21BC72A105KE01
D1, D2, D3, D4, D5: GS1010FL
EDGE1: 10046971-019LF
HA: IRLB3813NOHOLE; TO-220AB-NOHOLE
HB: IRLB3813NOHOLE; TO-220AB-NOHOLE
LA: IRLB3813NOHOLE; TO-220AB-NOHOLE
LB: IRLB3813NOHOLE; TO-220AB-NOHOLE
LED1, LED2, LED3, LED4, LED5: SML-E12V8WT86
R1, R4, R5, R6, R9, R11, R15, R16, R17, R18, R19, R24, R25: RG2012
R2: RG2012N-332-W-T1; RG2012
R3, R22: RG2012P-681-B-T5; RG2012
R7, R8, R26, R27: RG2012N-201-W-T1; RG2012
R10, R12, R20, R21: RG2012Q-100-D-T5; RG2012
R13: RG2012P-302-B-T5; RG2012
R14: RG2012N-222-W-T1; RG2012
RESET: THAF01-NC-R
SA: TVAF06-A020B-R
SB: TVAF06-A020B-R
SW4: SS-12D00G3
TLP1, TLP2: TLP2366
TR1, TR2, TR3, TR4: 2SC3325

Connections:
/DIR: A3921.19, D3.A, R17.RIGHT, TR4.C
/DIR_IN: EDGE1.P$26, R26.RIGHT
/FF1: A3921.25, R4.LEFT, TR1.B
/FF2: A3921.26, R5.LEFT, TR2.B
/GHA: A3921.10, R21.RIGHT
/GHB: A3921.5, R12.LEFT
/GLA: A3921.12, R20.RIGHT
/GLB: A3921.3, R10.LEFT
/GND_IN: EDGE1.P$24, TLP1.3, TLP2.3
/LAP: D4.A, D5.A, R9.LEFT, R25.LEFT, SW4.C, TR3.B
/PWM: A3921.23, R6.RIGHT, TR3.C
/PWM_IN: EDGE1.P$25, R27.RIGHT
/RESET: A3921.24, R11.LEFT, RESET.3
/SA: A3921.11, C8.P$2, EDGE1.P$1, EDGE1.P$2, EDGE1.P$3, EDGE1.P$4, EDGE1.P$5, EDGE1.P$45, EDGE1.P$46, EDGE1.P$47, EDGE1.P$48, EDGE1.P$49, EDGE1.P$50, HA.SOURCE, LA.DRAIN, R3.LEFT, R16.LEFT
/SB: A3921.4, C7.P$2, EDGE1.P$6, EDGE1.P$7, EDGE1.P$8, EDGE1.P$9, EDGE1.P$10, EDGE1.P$11, EDGE1.P$40, EDGE1.P$41, EDGE1.P$42, EDGE1.P$43, EDGE1.P$44, HB.SOURCE, LB.DRAIN, LED1.K, LED2.A, R19.LEFT
/V5: A3921.20, A3921.21, A3921.22, C1.P$2, C2.P$2, C3.P$2, R4.RIGHT, R5.RIGHT, R6.LEFT, R7.LEFT, R8.LEFT, R14.LEFT, R17.LEFT, TLP1.6, TLP2.6
GND: A3921.2, A3921.17, A3921.PAD, C1.P$1, C2.P$1, C3.P$1, C4.P$1, C5.P$1, C9.P$2, C10.C, C11.C, C12.P$2, C13.P$2, EDGE1.P$28, EDGE1.P$29, EDGE1.P$30, EDGE1.P$31, EDGE1.P$32, EDGE1.P$33, EDGE1.P$34, EDGE1.P$35, EDGE1.P$36, EDGE1.P$37, EDGE1.P$38, EDGE1.P$39, LA.SOURCE, LB.SOURCE, LED3.K, R2.RIGHT, R13.RIGHT, R15.LEFT, R18.LEFT, R24.RIGHT, R25.RIGHT, RESET.1, SA.LEFT, SB.RIGHT, SW4.R, TLP1.4, TLP2.4, TR1.E, TR2.E, TR3.E, TR4.E
unnamed: A3921.8, C4.P$2, C9.P$1
unnamed: A3921.13, C5.P$2, D1.C
unnamed: A3921.15, C6.P$1
unnamed: A3921.16, C6.P$2
unnamed: A3921.6, C7.P$1
unnamed: A3921.9, C8.P$1
unnamed: D2.A, R1.LEFT, R24.LEFT, TR4.B
unnamed: D2.C, D4.C, SA.RIGHT
unnamed: D3.C, D5.C, SB.LEFT
unnamed: HA.GATE, R16.RIGHT, R21.LEFT
unnamed: HB.GATE, R12.RIGHT, R19.RIGHT
unnamed: A3921.27, R13.LEFT
unnamed: A3921.28, R2.LEFT, R14.RIGHT
unnamed: LA.GATE, R15.RIGHT, R20.LEFT
unnamed: LB.GATE, R10.RIGHT, R18.RIGHT
unnamed: LED1.A, LED2.K, R3.RIGHT
unnamed: LED3.A, R22.RIGHT
unnamed: LED4.A, R7.RIGHT
unnamed: LED4.K, TR1.C
unnamed: LED5.A, R8.RIGHT
unnamed: LED5.K, TR2.C
unnamed: R1.RIGHT, TLP1.5
unnamed: R9.RIGHT, TLP2.5
unnamed: R26.LEFT, TLP1.1
unnamed: R27.LEFT, TLP2.1
VCC: A3921.1, C10.A, C11.A, C12.P$1, C13.P$1, D1.A, EDGE1.P$12, EDGE1.P$13, EDGE1.P$14, EDGE1.P$15, EDGE1.P$16, EDGE1.P$17, EDGE1.P$18, EDGE1.P$19, EDGE1.P$20, EDGE1.P$21, EDGE1.P$22, EDGE1.P$23, HA.DRAIN, HB.DRAIN, R11.RIGHT, R22.LEFT

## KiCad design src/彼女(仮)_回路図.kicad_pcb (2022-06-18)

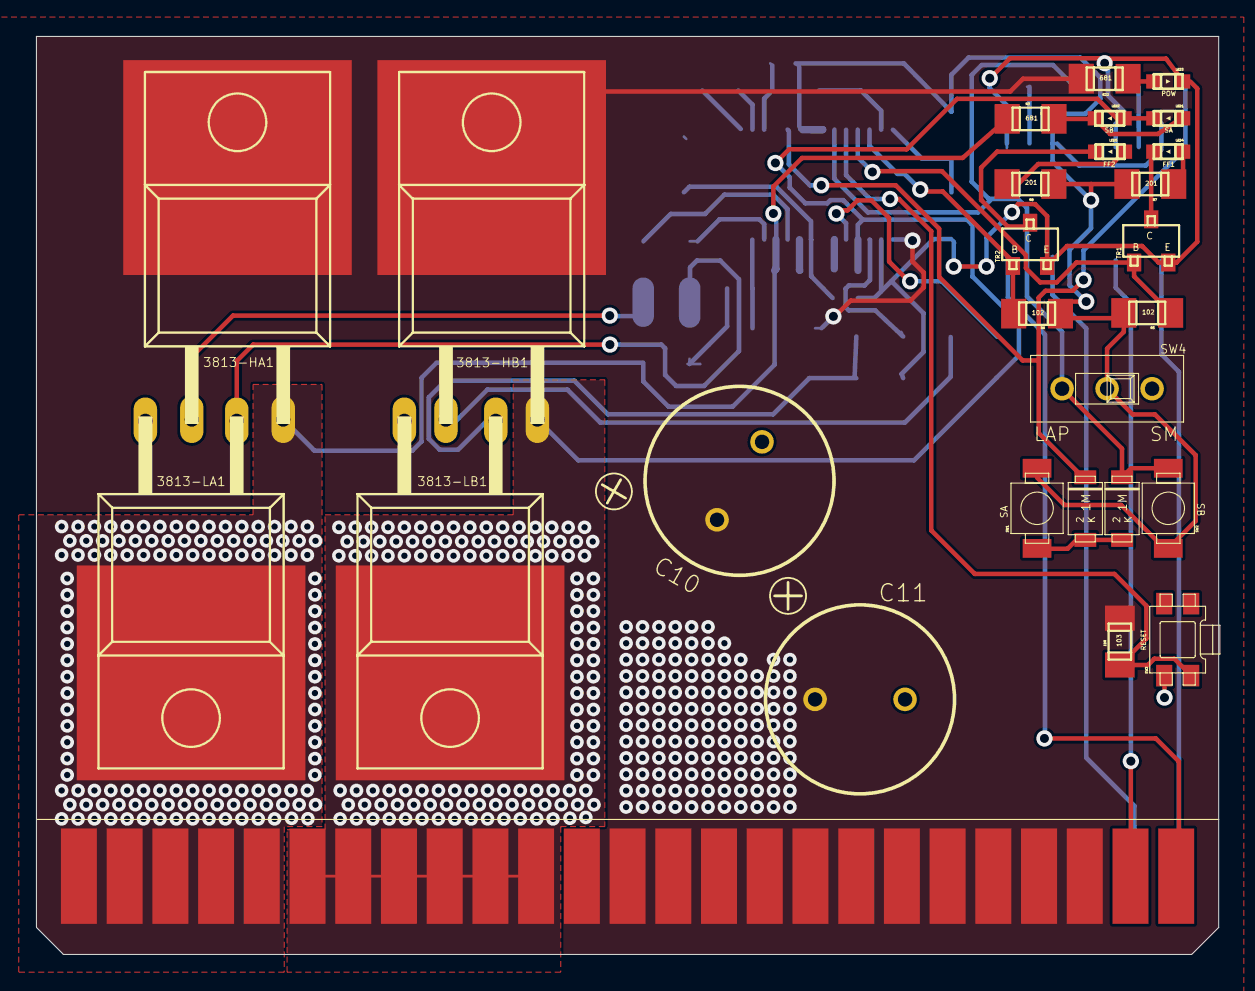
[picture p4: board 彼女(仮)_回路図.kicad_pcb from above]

Board: 2 copper layers, 65.7 x 51.0 mm, 55 parts (0 on the bottom side), 39 nets.

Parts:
3813-HA1, 3813-HB1, 3813-LA1, 3813-LB1: IRLB3813NOHOLE; TO-220AB-NOHOLE
C1, C2, C3, C4, C5, C7, C8: GCM188L81H104KA57
C6: GCM21BR71H474KA55
C9: GRT31CC81H225KE01L
C10, C11: 35PZJ330M10X9
C12: GRM32ER7YA106KA12
C13: GRM21BC72A105KE01
D1, D8, D9: GS1010FL
EDGE1: 10046971-019LF
IC1: A3921
LED1, LED2, LED3, LED4, LED5: SML-E12V8WT86
R1, R9, R11, R15, R16, R18, R19: RG2012
R2: RG2012N-332-W-T1; RG2012
R3, R22: RG2012P-681-B-T5; RG2012
R5, R6: RG2012-N-102-B-T5; RG2012
R7, R8: RG2012N-201-W-T1; RG2012
R10, R12, R20, R21: RG2012Q-100-D-T5; RG2012
R13: RG2012P-302-B-T5; RG2012
R14: RG2012N-222-W-T1; RG2012
SW1, SW2: TVAF06-A020B-R
SW3: THAF01-NC-R
SW4: SS-12D00G3
TLP1, TLP2: TLP2366
TR1, TR2: 2SC3325

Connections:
/DIR: D8.C, IC1.19, R1.LEFT
/DIR_IN: EDGE1.P$26, TLP1.1
/FF1: IC1.25, R5.RIGHT, TR1.B
/FF2: IC1.26, R6.RIGHT, TR2.B
/GHA: IC1.10, R21.RIGHT
/GHB: IC1.5, R12.LEFT
/GLA: IC1.12, R20.RIGHT
/GLB: IC1.3, R10.LEFT
/GND_IN: EDGE1.P$24, TLP1.3
/PWM: D9.C, IC1.23, R9.LEFT, SW2.LEFT, SW4.R
/PWM_IN: EDGE1.P$25, TLP2.3
/RESET: IC1.24, R11.LEFT, SW3.3
/SA: 3813-HA1.SOURCE, 3813-LA1.DRAIN, C8.P$2, EDGE1.P$1, EDGE1.P$2, EDGE1.P$3, EDGE1.P$4, EDGE1.P$5, EDGE1.P$45, EDGE1.P$46, EDGE1.P$47, EDGE1.P$48, EDGE1.P$49, EDGE1.P$50, IC1.11, R3.LEFT, R16.LEFT
/SB: 3813-HB1.SOURCE, 3813-LB1.DRAIN, C7.P$2, EDGE1.P$6, EDGE1.P$7, EDGE1.P$8, EDGE1.P$9, EDGE1.P$10, EDGE1.P$11, EDGE1.P$40, EDGE1.P$41, EDGE1.P$42, EDGE1.P$43, EDGE1.P$44, IC1.4, LED1.K, LED2.A, R19.LEFT
/V5: C1.P$2, C2.P$2, C3.P$2, IC1.20, IC1.21, IC1.22, R5.LEFT, R6.LEFT, R7.LEFT, R8.LEFT, R14.LEFT, SW1.LEFT, SW2.RIGHT, SW4.C, TLP1.6, TLP2.6
/VCC_IN: EDGE1.P$27, TLP2.1
GND: 3813-LA1.SOURCE, 3813-LB1.SOURCE, C1.P$1, C2.P$1, C3.P$1, C4.P$1, C5.P$1, C9.P$2, C10.C, C11.C, C12.P$2, C13.P$2, EDGE1.P$28, EDGE1.P$29, EDGE1.P$30, EDGE1.P$31, EDGE1.P$32, EDGE1.P$33, EDGE1.P$34, EDGE1.P$35, EDGE1.P$36, EDGE1.P$37, EDGE1.P$38, EDGE1.P$39, IC1.2, IC1.17, LED3.K, R2.RIGHT, R13.RIGHT, R15.LEFT, R18.LEFT, SW3.1, TLP1.4, TLP2.4, TR1.E, TR2.E
unnamed: 3813-HA1.GATE, R16.RIGHT, R21.LEFT
unnamed: 3813-HB1.GATE, R12.RIGHT, R19.RIGHT
unnamed: 3813-LA1.GATE, R15.RIGHT, R20.LEFT
unnamed: 3813-LB1.GATE, R10.RIGHT, R18.RIGHT
unnamed: C4.P$2, C9.P$1, IC1.8
unnamed: C5.P$2, D1.C, IC1.13
unnamed: C6.P$1, IC1.15
unnamed: C6.P$2, IC1.16
unnamed: C7.P$1, IC1.6
unnamed: C8.P$1, IC1.9
unnamed: D8.A, D9.A, SW1.RIGHT
unnamed: IC1.27, R13.LEFT
unnamed: IC1.28, R2.LEFT, R14.RIGHT
unnamed: LED1.A, LED2.K, R3.RIGHT
unnamed: LED3.A, R22.RIGHT
unnamed: LED4.A, R7.RIGHT
unnamed: LED4.K, TR1.C
unnamed: LED5.A, R8.RIGHT
unnamed: LED5.K, TR2.C
unnamed: R1.RIGHT, TLP1.5
unnamed: R9.RIGHT, TLP2.5
VCC: 3813-HA1.DRAIN, 3813-HB1.DRAIN, C10.A, C11.A, C12.P$1, C13.P$1, D1.A, EDGE1.P$12, EDGE1.P$13, EDGE1.P$14, EDGE1.P$15, EDGE1.P$16, EDGE1.P$17, EDGE1.P$18, EDGE1.P$19, EDGE1.P$20, EDGE1.P$21, EDGE1.P$22, EDGE1.P$23, IC1.1, R11.RIGHT, R22.LEFT

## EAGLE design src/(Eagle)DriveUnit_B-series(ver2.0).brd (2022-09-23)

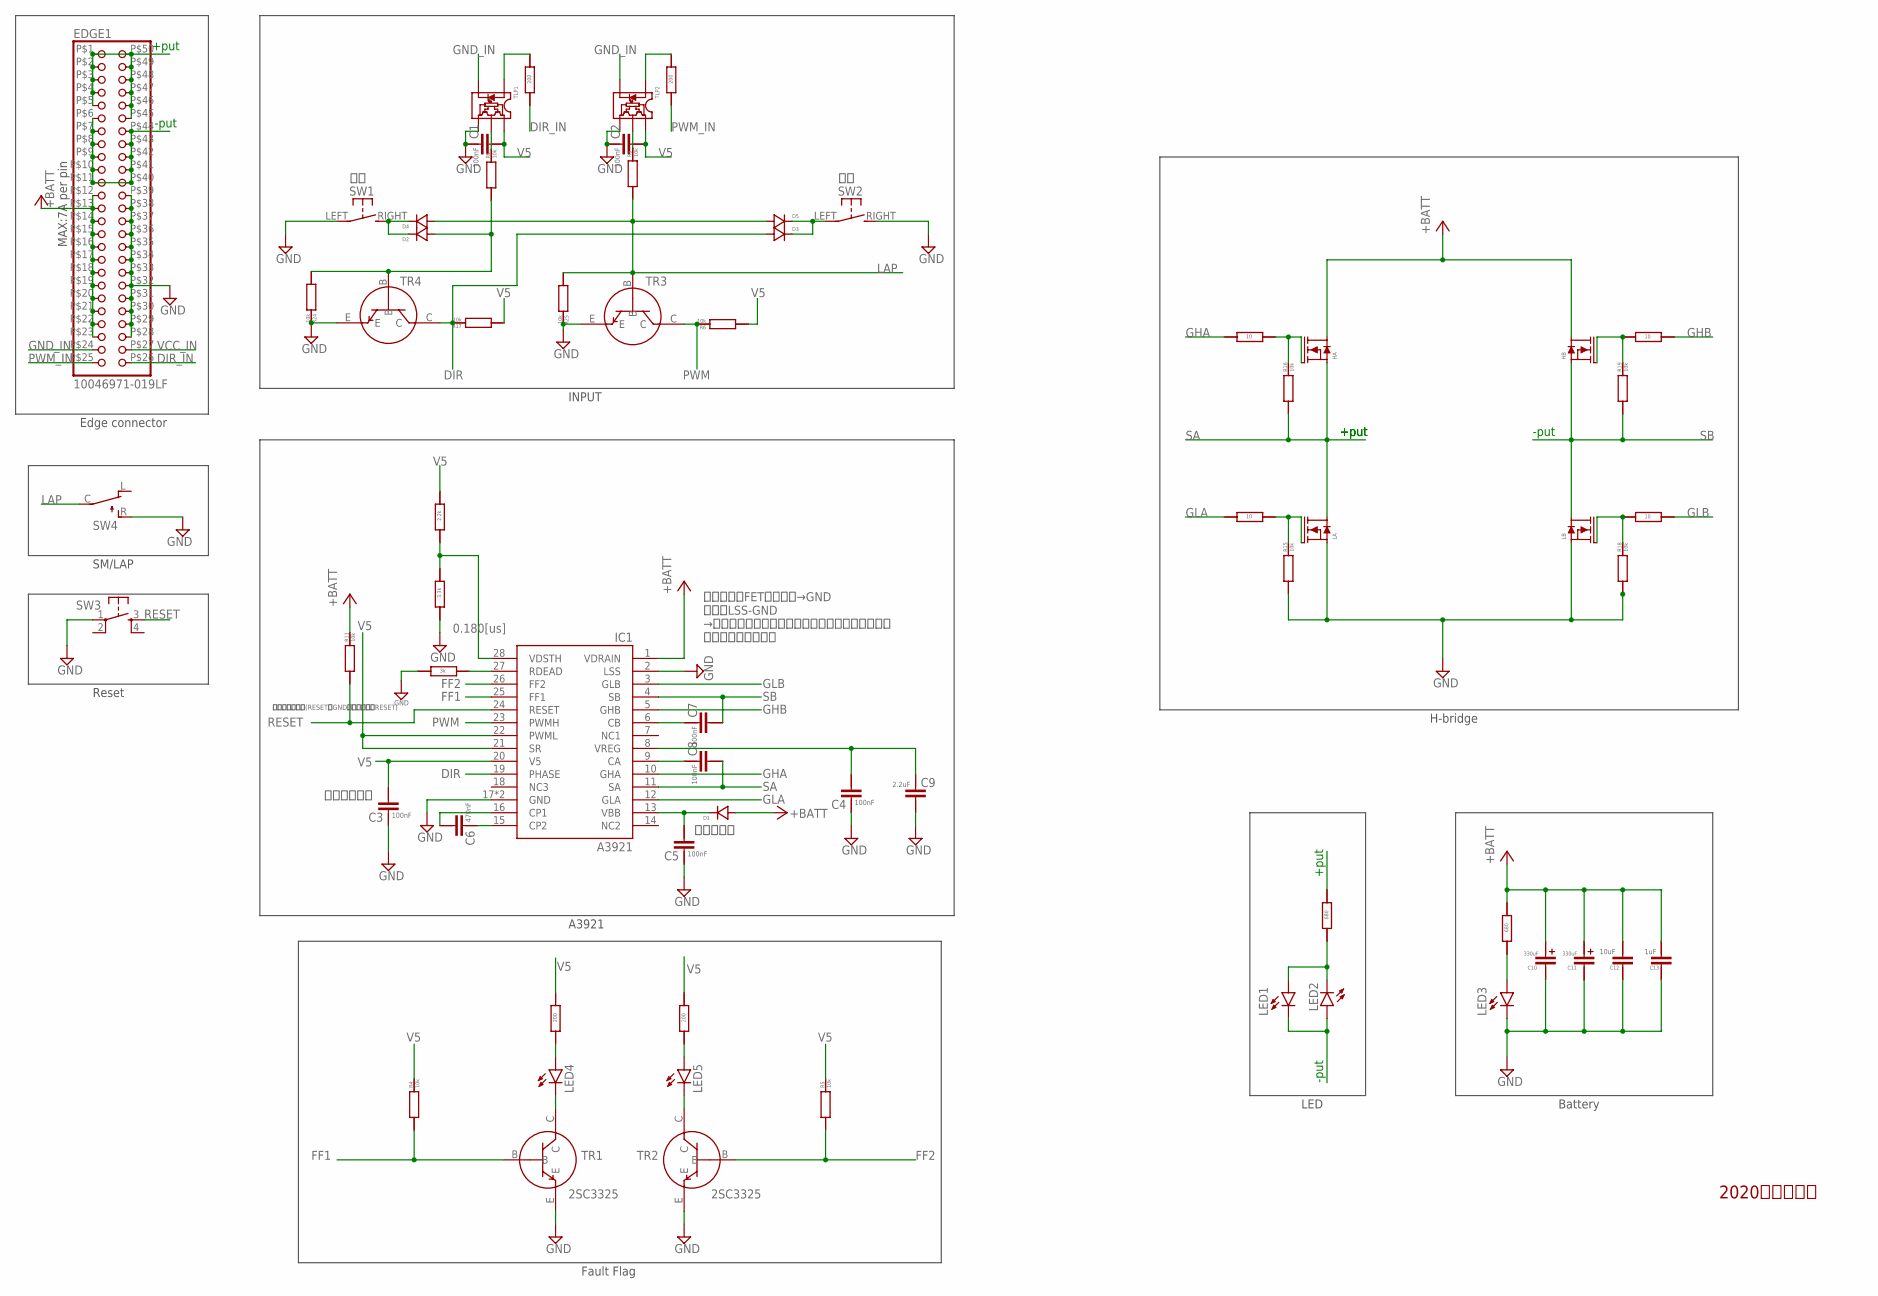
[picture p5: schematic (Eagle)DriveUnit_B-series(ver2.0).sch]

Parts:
C1, C2, C3, C4, C5, C7, C8: GCM188L81H104KA57
C6: GCM21BR71H474KA55
C9: GRT31CC81H225KE01L
C10, C11: 35PZJ330M10X9
C12: GRM32ER7YA106KA12
C13: GRM21BC72A105KE01
D1, D2, D3, D4, D5: GS1010FL
EDGE1: 10046971-019LF
HA: IRLB3813NOHOLE; TO-220AB-NOHOLE
HB: IRLB3813NOHOLE; TO-220AB-NOHOLE
IC1: A3921
LA: IRLB3813NOHOLE; TO-220AB-NOHOLE
LB: IRLB3813NOHOLE; TO-220AB-NOHOLE
LED1, LED2, LED3, LED4, LED5: SML-E12V8WT86
R1, R4, R5, R6, R9, R11, R15, R16, R17, R18, R19, R24, R25: RG2012
R2: RG2012N-332-W-T1; RG2012
R3, R22: RG2012P-681-B-T5; RG2012
R7, R8, R26, R27: RG2012N-201-W-T1; RG2012
R10, R12, R20, R21: RG2012Q-100-D-T5; RG2012
R13: RG2012P-302-B-T5; RG2012
R14: RG2012N-222-W-T1; RG2012
SW1, SW2: TVAF06-A020B-R
SW3: THAF01-NC-R
SW4: SS-12D00G3
TLP1, TLP2: TLP2366
TR1, TR2, TR3, TR4: 2SC3325

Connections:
DIR: D3.A, IC1.19 (PHASE), R17.RIGHT, TR4.C
DIR_IN: EDGE1.P$26 (P26), R26.RIGHT
FF1: IC1.25 (FF1), R4.LEFT, TR1.B
FF2: IC1.26 (FF2), R5.LEFT, TR2.B
GHA: IC1.10 (GHA), R21.RIGHT
GHB: IC1.5 (GHB), R12.LEFT
GLA: IC1.12 (GLA), R20.RIGHT
GLB: IC1.3 (GLB), R10.LEFT
GND: C1.P$1, C2.P$1, C3.P$1, C4.P$1, C5.P$1, C9.P$2, C10.C (CATHODE), C11.C (CATHODE), C12.P$2, C13.P$2, EDGE1.P$28 (P28), EDGE1.P$29 (P29), EDGE1.P$30 (P30), EDGE1.P$31 (P31), EDGE1.P$32 (P32), EDGE1.P$33 (P33), EDGE1.P$34 (P34), EDGE1.P$35 (P35), EDGE1.P$36 (P36), EDGE1.P$37 (P37), EDGE1.P$38 (P38), EDGE1.P$39 (P39), IC1.2 (LSS), IC1.17 (GND), IC1.PAD (GND), LA.SOURCE (S), LB.SOURCE (S), LED3.K (C), R2.RIGHT, R13.RIGHT, R15.LEFT, R18.LEFT, R24.RIGHT, R25.RIGHT, SW1.LEFT, SW2.RIGHT (S), SW3.1, SW4.R, TLP1.4 (GND), TLP2.4 (GND), TR1.E, TR2.E, TR3.E, TR4.E
GND_IN: EDGE1.P$24 (P24), TLP1.3 (CATHODE), TLP2.3 (CATHODE)
LAP: D4.A, D5.A, R9.LEFT, R25.LEFT, SW4.C, TR3.B
unnamed: C6.P$1, IC1.15 (CP2)
unnamed: C6.P$2, IC1.16 (CP1)
unnamed: C7.P$1, IC1.6 (CB)
unnamed: IC1.28 (VDSTH), R2.LEFT, R14.RIGHT
unnamed: LED4.K (C), TR1.C
unnamed: C4.P$2, C9.P$1, IC1.8 (VREG)
unnamed: C5.P$2, D1.C, IC1.13 (VBB)
unnamed: LED5.K (C), TR2.C
unnamed: LED4.A, R7.RIGHT
unnamed: LED5.A, R8.RIGHT
unnamed: R1.RIGHT, TLP1.5 (VOUT)
unnamed: D2.C, D4.C, SW1.RIGHT (S)
unnamed: HA.GATE (G), R16.RIGHT, R21.LEFT
unnamed: R9.RIGHT, TLP2.5 (VOUT)
unnamed: C8.P$1, IC1.9 (CA)
unnamed: D2.A, R1.LEFT, R24.LEFT, TR4.B
unnamed: LED1.A, LED2.K (C), R3.RIGHT
unnamed: IC1.27 (RDEAD), R13.LEFT
unnamed: D3.C, D5.C, SW2.LEFT
unnamed: HB.GATE (G), R12.RIGHT, R19.RIGHT
unnamed: LED3.A, R22.RIGHT
unnamed: R26.LEFT, TLP1.1 (ANODE)
unnamed: R27.LEFT, TLP2.1 (ANODE)
unnamed: LA.GATE (G), R15.RIGHT, R20.LEFT
unnamed: LB.GATE (G), R10.RIGHT, R18.RIGHT
PWM: IC1.23 (PWMH), R6.RIGHT, TR3.C
PWM_IN: EDGE1.P$25 (P25), R27.RIGHT
RESET: IC1.24 (RESET), R11.LEFT, SW3.3
SA: C8.P$2, EDGE1.P$1 (P1), EDGE1.P$2 (P2), EDGE1.P$3 (P3), EDGE1.P$4 (P4), EDGE1.P$5 (P5), EDGE1.P$45 (P45), EDGE1.P$46 (P46), EDGE1.P$47 (P47), EDGE1.P$48 (P48), EDGE1.P$49 (P49), EDGE1.P$50 (P50), HA.SOURCE (S), IC1.11 (SA), LA.DRAIN (D), R3.LEFT, R16.LEFT
SB: C7.P$2, EDGE1.P$6 (P6), EDGE1.P$7 (P7), EDGE1.P$8 (P8), EDGE1.P$9 (P9), EDGE1.P$10 (P10), EDGE1.P$11 (P11), EDGE1.P$40 (P40), EDGE1.P$41 (P41), EDGE1.P$42 (P42), EDGE1.P$43 (P43), EDGE1.P$44 (P44), HB.SOURCE (S), IC1.4 (SB), LB.DRAIN (D), LED1.K (C), LED2.A, R19.LEFT
V5: C1.P$2, C2.P$2, C3.P$2, IC1.20 (V5), IC1.21 (SR), IC1.22 (PWML), R4.RIGHT, R5.RIGHT, R6.LEFT, R7.LEFT, R8.LEFT, R14.LEFT, R17.LEFT, TLP1.6 (VCC), TLP2.6 (VCC)
VCC: C10.A (ANODE), C11.A (ANODE), C12.P$1, C13.P$1, D1.A, EDGE1.P$12 (P12), EDGE1.P$13 (P13), EDGE1.P$14 (P14), EDGE1.P$15 (P15), EDGE1.P$16 (P16), EDGE1.P$17 (P17), EDGE1.P$18 (P18), EDGE1.P$19 (P19), EDGE1.P$20 (P20), EDGE1.P$21 (P21), EDGE1.P$22 (P22), EDGE1.P$23 (P23), HA.DRAIN (D), HB.DRAIN (D), IC1.1 (VDRAIN), R11.RIGHT, R22.LEFT
VCC_IN: EDGE1.P$27 (P27)

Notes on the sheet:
2020年度回路班
RESET
GLB
GHB
FF2
FF1
ローサイドFETのソース→GND 従ってLSS-GND →と思ったがノイズを産む可能性があるためできる だけソースと繋げる
逆電圧防止
パスコンくん
プルアップ抵抗(RESETをGNDに接続するとRESET)
0.180[us]
+put
-put
H-bridge
LED
Battery
Edge connector
A3921
Fault Flag
INPUT
SM/LAP
Reset

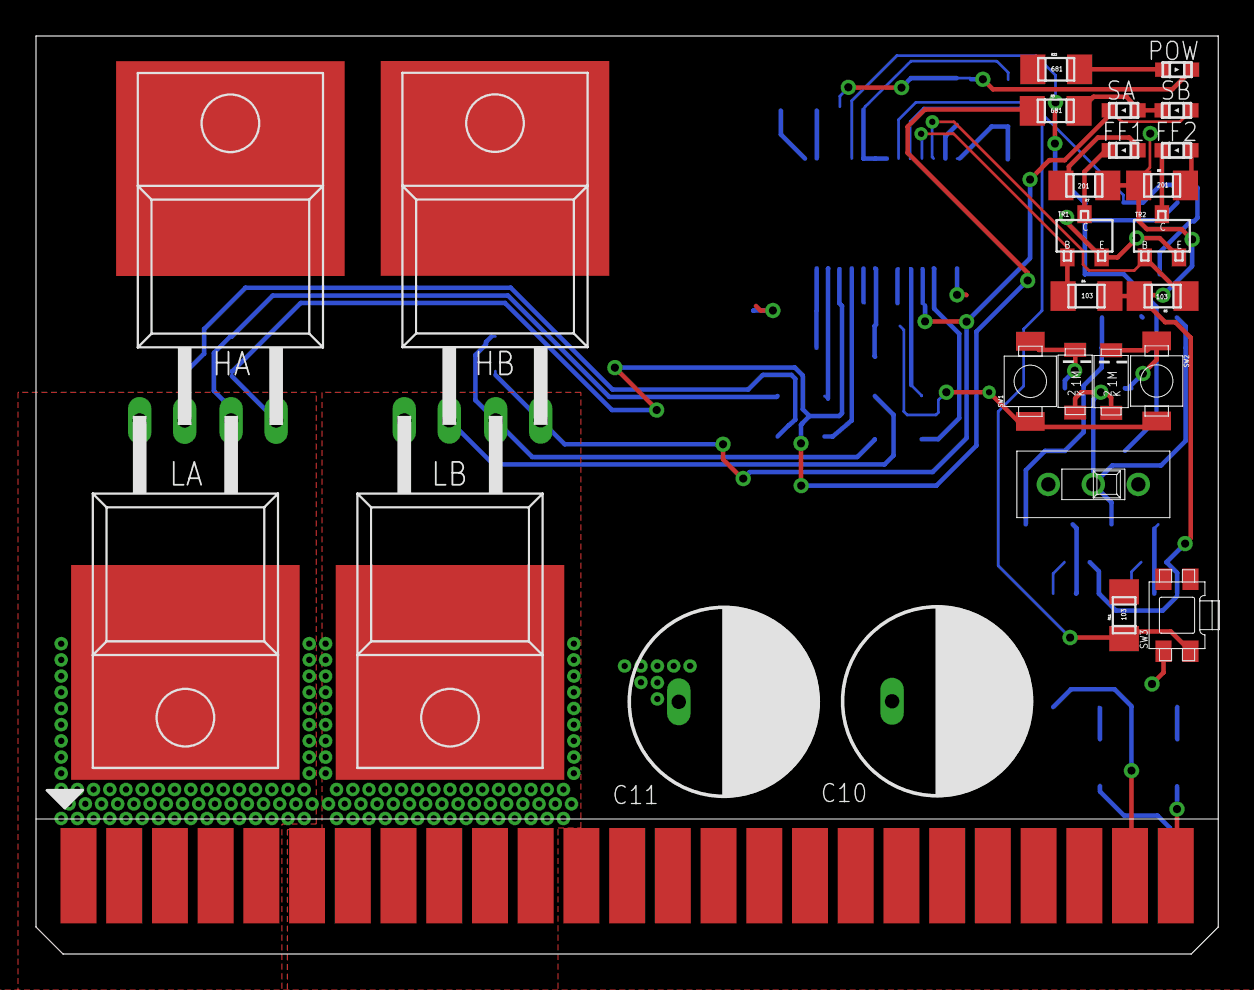
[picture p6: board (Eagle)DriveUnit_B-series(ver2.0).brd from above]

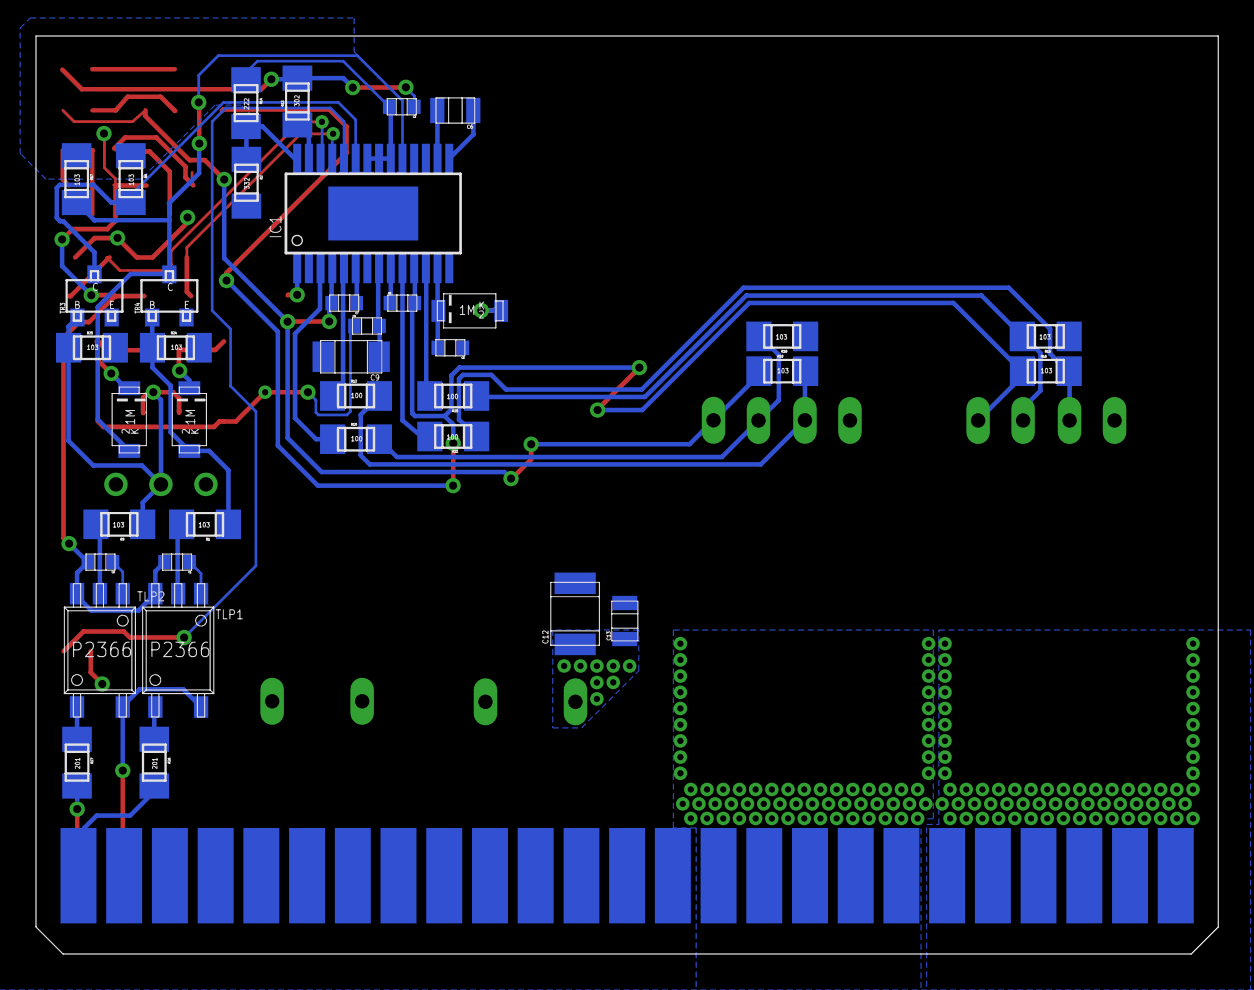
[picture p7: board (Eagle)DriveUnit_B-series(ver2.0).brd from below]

Board: 2 copper layers, 65.7 x 51.0 mm, 65 parts (38 on the bottom side), 43 nets.

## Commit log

2022-05-15 brd編集 配線
    [彼女(仮)_回路図.brd]
2022-05-17 部品配置訂正 大電流パターン考慮
    [彼女(仮)_回路図.brd]
2022-05-17 edit:配線の追加
    [彼女(仮)_回路図.brd]
2022-05-18 edit:GND,VCCベタ,wireの追加
    [彼女(仮)_回路図.brd, 彼女(仮)_回路図.sch]
2022-05-19 edit:大体配線完了
    [彼女(仮)_回路図.brd, 彼女(仮)_回路図.sch]
2022-05-23 ビアの配置
    [彼女(仮)_回路図.brd]
2022-05-25 ビア,パターンの追加 ほぼ完成
    [彼女(仮)_回路図.brd, 彼女(仮)_回路図.sch]
2022-05-29 GNDパターンの強化
    [彼女(仮)_回路図.brd]
2022-06-15 配線の追加,整理
    [彼女(仮)_回路図.brd]
2022-06-16 配線を太くした
    [彼女(仮)_回路図.brd]
2022-06-17 配線完了
    [彼女(仮)_回路図.brd]
2022-06-17 KiCadへの移行,PCBデザインの完成
    [彼女(仮)_回路図.brd, 彼女(仮)_回路図.kicad_pcb, 彼女(仮)_回路図.sch]
2022-06-18 配線の修正等
    [彼女(仮)_回路図.kicad_pcb]
2022-06-18 DRCエラーの対処
    [彼女(仮)_回路図.kicad_pcb]
2022-06-23 基板デザインの完成
    [DriveUnit_Bseries.kicad_pcb]
2022-06-24 Update README.md
    部品のリストを更新
2022-06-24 Update README.md
    使用電子部品，及びその値段の表の追加
2022-06-24 Update README.md
    総額の追加
2022-06-24 Update README.md
    前モタドラとの違いを記述
2022-06-25 Update README.md
    回路図の追加
2022-06-25 gerberの出力,名前の変更
    [DriveUnit_B-series(ver1.0)-B_Mask.gbr, DriveUnit_B-series(ver1.0)-B_Paste.gbr, DriveUnit_B-series(ver1.0)-B_SilkS.gbr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]
2022-06-25 fp-info-cacheの更新
    [DriveUnit_B-series(ver1.0).brd, DriveUnit_B-series(ver1.0).kicad_pcb]
2022-06-26 名前の変更
    [DriveUnit_B-series(ver1.0).sch, DriveUnit_Bseries.kicad_pcb]
2022-06-28 Update README.md
    回路図のクローン方法の追加
2022-06-30 Eagle_ERCエラーの修復
2022-06-30 Update README.md
    説明の追加
2022-06-30 Update README.md
    linkの更新
2022-07-01 意図的なconflict
    [DriveUnit_B-series(ver1.0).kicad_pcb]
2022-07-01 conflict前段階
    [DriveUnit_B-series(ver1.0).brd, DriveUnit_B-series(ver1.0).kicad_pcb]
2022-07-01 意図conflict new側
    [DriveUnit_B-series(ver1.0).kicad_pcb]
2022-07-01 背面パッドの考慮
    [DriveUnit_B-series(ver1.0).kicad_pcb]
2022-07-01 conflict解消 サーマルパッドの考慮
    [DriveUnit_B-series(ver1.0).kicad_pcb]
2022-07-01 gerberの更新
    [DriveUnit_B-series(ver1.0)-B_Mask.gbr, DriveUnit_B-series(ver1.0)-B_Paste.gbr, DriveUnit_B-series(ver1.0)-B_SilkS.gbr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]
2022-07-01 Update .gitignore
    Eagleの追加
2022-07-02 GNDベタの修正
    [DriveUnit_B-series(ver1.0)-B_Mask.gbr, DriveUnit_B-series(ver1.0)-B_Paste.gbr, DriveUnit_B-series(ver1.0)-B_SilkS.gbr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]
2022-07-02 ガバ設計による炎上回避(GNDベタを大きくした)
    [DriveUnit_B-series(ver1.0)-B_Mask.gbr, DriveUnit_B-series(ver1.0)-B_Paste.gbr, DriveUnit_B-series(ver1.0)-B_SilkS.gbr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]
2022-07-02 シルクの修正
    [DriveUnit_B-series(ver1.0)-B_Mask.gbr, DriveUnit_B-series(ver1.0)-B_Paste.gbr, DriveUnit_B-series(ver1.0)-B_SilkS.gbr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]
2022-07-02 Update README.md
    FFXピンの説明
2022-07-03 FF2の配線の修正
    [DriveUnit_B-series(ver1.0)-B_Mask.gbr, DriveUnit_B-series(ver1.0)-B_Paste.gbr, DriveUnit_B-series(ver1.0)-B_SilkS.gbr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]
2022-07-05 フォトカプラLED入力に200ohm抵抗付けた
    [(Eagle)DriveUnit_B-series(ver1.0).brd, (Eagle)DriveUnit_B-series(ver1.0).sch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]
2022-07-05 Update README.md
    表の画像の修正
2022-07-06 Update README.md
    R4，R17の追加
2022-07-09 Update README.md
    ページの追加，敬語
2022-07-11 Update README.md
    機能の説明の追加
2022-08-05 readme.mdの編集
2022-08-05 折りたたみの追加
2022-08-06 readme.mdに不具合の追加
2022-08-06 Update README.md
    ミスの修正
2022-08-08 Update README.md
    修正点の追加
2022-08-11 はんだ付けの仕方の説明の追加
2022-08-12 read.me更新
2022-08-12 readme.mdの更新
2022-08-14 ヒートガンリフローの説明の追加
2022-08-14 はんだ付けの説明終了
2022-08-30 [fix]入力周りなどの変更(ver1.0の問題点の修復)
    [(Eagle)DriveUnit_B-series(ver1.0).brd, (Eagle)DriveUnit_B-series(ver1.0).sch]
2022-09-01 入力部分の追加
    [(Eagle)DriveUnit_B-series(ver2.0).brd, (Eagle)DriveUnit_B-series(ver2.0).sch]
2022-09-01 README_v1等の追加
2022-09-01 回路図の偏向
    [(Eagle)DriveUnit_B-series(ver2.0).sch]
2022-09-02 [fix]デッドタイムを100kΩ可変抵抗で調整できるように変更
    [(Eagle)DriveUnit_B-series(ver2.0).brd, (Eagle)DriveUnit_B-series(ver2.0).sch]
2022-09-02 [add]電流センサ周りの配線_1
    [(Eagle)DriveUnit_B-series(ver2.0).brd, (Eagle)DriveUnit_B-series(ver2.0).sch]
2022-09-15 [remove:電流センサを取り除いた
    [(Eagle)DriveUnit_B-series(ver2.0).brd, (Eagle)DriveUnit_B-series(ver2.0).sch]
2022-09-15 [add]配線の追加
    [(Eagle)DriveUnit_B-series(ver2.0).sch]
2022-09-16 入力部の配線の追加
    [(Eagle)DriveUnit_B-series(ver2.0).brd, (Eagle)DriveUnit_B-series(ver2.0).sch]
2022-09-16 [add]部品配置完了
    [(Eagle)DriveUnit_B-series(ver2.0).brd]
2022-09-16 [add]9/16進捗分
    [(Eagle)DriveUnit_B-series(ver2.0).brd]
2022-09-18 配線の追加
    [(Eagle)DriveUnit_B-series(ver2.0).brd, (Eagle)DriveUnit_B-series(ver2.0).sch]
2022-09-19 ビアなどの追加
    [(Eagle)DriveUnit_B-series(ver2.0).brd]
2022-09-19 SA，SBベタ以外は配線終了．
    [(Eagle)DriveUnit_B-series(ver2.0).brd]
2022-09-20 配線の終了
    [(Eagle)DriveUnit_B-series(ver2.0).brd]
2022-09-20 モタドラ配線完全終了_KiCad移行前
    [(Eagle)DriveUnit_B-series(ver2.0).brd]
2022-09-20 kicad完全移行_シルク配置全完
    [(KiCad)DriveUnit_B-series(ver2.0).kicad_pcb, (KiCad)DriveUnit_B-series(ver2.0).sch, DriveUnit_B-series(ver1.0).kicad_pcb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]
2022-09-20 デザイン完了
    [(KiCad)DriveUnit_B-series(ver2.0).kicad_pcb]
2022-09-21 ver2.0完全完了_gerber出力前
    [(KiCad)DriveUnit_B-series(ver2.0).kicad_pcb]
2022-09-21 ver2.0ちょい修正_gerber出力前
    [(KiCad)DriveUnit_B-series(ver2.0).kicad_pcb]
2022-09-21 gerber出力完了
    [(KiCad)DriveUnit_B-series(ver2.0)-B_Mask.gbr, (KiCad)DriveUnit_B-series(ver2.0)-B_Paste.gbr, (KiCad)DriveUnit_B-series(ver2.0)-B_SilkS.gbr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]
2022-09-22 回路ミスってた(嘘だろ...)_KiCad以降前
    [(Eagle)DriveUnit_B-series(ver2.0).brd, (Eagle)DriveUnit_B-series(ver2.0).sch]
2022-09-22 修正前ファイルを消した_KiCad以降前
    [(KiCad)DriveUnit_B-series(ver2.0)-B_Mask.gbr, (KiCad)DriveUnit_B-series(ver2.0)-B_Paste.gbr, (KiCad)DriveUnit_B-series(ver2.0)-B_SilkS.gbr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]
2022-09-22 KiCad移行後_schファイル破壊
    [(Eagle)DriveUnit_B-series(ver2.0).kicad_pcb, (Eagle)DriveUnit_B-series(ver2.0).sch]
2022-09-22 KiCad移行後_破壊ファイルの修正
    [(Eagle)DriveUnit_B-series(ver2.0).sch, (KiCad)DriveUnit_B-series(ver2.0).kicad_pcb, (KiCad)DriveUnit_B-series(ver2.0).sch]
2022-09-22 表デザイン完成
    [(KiCad)DriveUnit_B-series(ver2.0).kicad_pcb]
2022-09-22 デザイン途中まで
    [(KiCad)DriveUnit_B-series(ver2.0).kicad_pcb]
2022-09-23 基板デザインの完全完成_gerber出力前
    [(KiCad)DriveUnit_B-series(ver2.0).kicad_pcb]
2022-09-23 gerber出力後
    [(KiCad)DriveUnit_B-series(ver2.0)-B_Mask.gbr, (KiCad)DriveUnit_B-series(ver2.0)-B_Paste.gbr, (KiCad)DriveUnit_B-series(ver2.0)-B_SilkS.gbr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]
2022-09-23 gerber出力 一応もう一回(え？)
    [(KiCad)DriveUnit_B-series(ver2.0)-B_Mask.gbr, (KiCad)DriveUnit_B-series(ver2.0)-B_Paste.gbr, (KiCad)DriveUnit_B-series(ver2.0)-B_SilkS.gbr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]
2022-09-24 readmeの更新
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

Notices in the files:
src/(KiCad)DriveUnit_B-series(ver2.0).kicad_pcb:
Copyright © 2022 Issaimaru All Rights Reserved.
